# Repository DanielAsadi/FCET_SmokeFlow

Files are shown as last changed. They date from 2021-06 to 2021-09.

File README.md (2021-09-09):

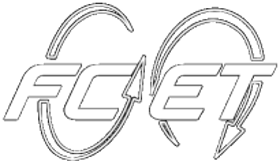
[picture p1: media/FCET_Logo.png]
#  Smoke Flow Visualization Setup
This set of code is for the control of the smoke flow visualization experimental setup at the FCET lab wind tunnel in UTIAS. 
Using an Arduino which receives input from the user or active grid encoder, the circuit outputs timed controls to the valve, heated nichrome wire and camera to create and photograph the smoke flow.

## Further Information
### [Project Information + Progress Document](https://docs.google.com/document/d/1TpjQxDYd5ZbAC--HKGrwxiYLXjzm-MVlI9GUeiGMbgY/edit?usp=sharing)
### [Project Presentation](https://docs.google.com/presentation/d/1Sq_wyhLVnCP48-y7gE646tIXf9qmjQ5rv_RyZEfXHPY/edit?usp=sharing)

### Project Abstract: Automation of a Wind Tunnel Smoke Flow Visualization (SFV) Rig
When analyzing the properties and features of flow around aerodynamic devices, there are quantitative techniques such as particle image velocimetry (PIV) and hot-wire anemometry, while the SFV method provides a simpler set-up and qualitative look at the flow field. The SFV technique consists of a nichrome wire that is coated in propylene glycol and is heated to create lines of smoke through the wind tunnel. It allows for the visual identification of key features such as boundary layers, laminar or turbulent flow and vortex shedding. Currently, each instrument in the setup is controlled manually and is only effective for flow speeds under 5 m/s, therefore limiting the precision of equipment usage for unsteady conditions and the range of possible cases to study. This project aims to increase the efficiency, precision, and versatility of the SFV setup by automating the components using a microcontroller, as well as implementing capacitors to rapidly discharge high levels of current for usage above 5 m/s. The desired circuit and code design will obtain inputs either from an encoder signal or a manual trigger and output precise, timed controls to the wire heating, the dispensing of propylene glycol, the camera, and the capacitors. Design solutions will be evaluated based on the metrics of usability, compatibility and responsiveness. Ultimately, this system maximized the usage of SFV and aided in the studies of laminar separation bubbles. Through iterative design and evaluation of metrics, the created design was able to produce informative images in a consistent manner while additions are being made to augment the usage of the instruments through the ability to read and save data.

## Code Structure
This code was operated using Ardino code which uses C++ and Python. The Arduino code controls the high/low signals and communication to the smoke flow instruments while the Python code controls the user interface and manual or automated control of these signals.

### Python Environment
This project uses the virutalenv Python environment. The Pyserial package is installed to communicate with the Arduino using Python. Matplotlib and Pandas packages are installed for encoder data graphing The commands below were used to create a virtual envrionment and install the additonal packages.
```
> pip install virtualenv
> python3 -m venv smokeflow
> smokeflow\Scripts\activate.bat
(smokeflow) > pip install pyserial
(smokeflow) > pip install matplotlib
(smokeflow) > pip install pandas
```
## Smoke Flow Circuit Diagram and Experimental Setup Photos
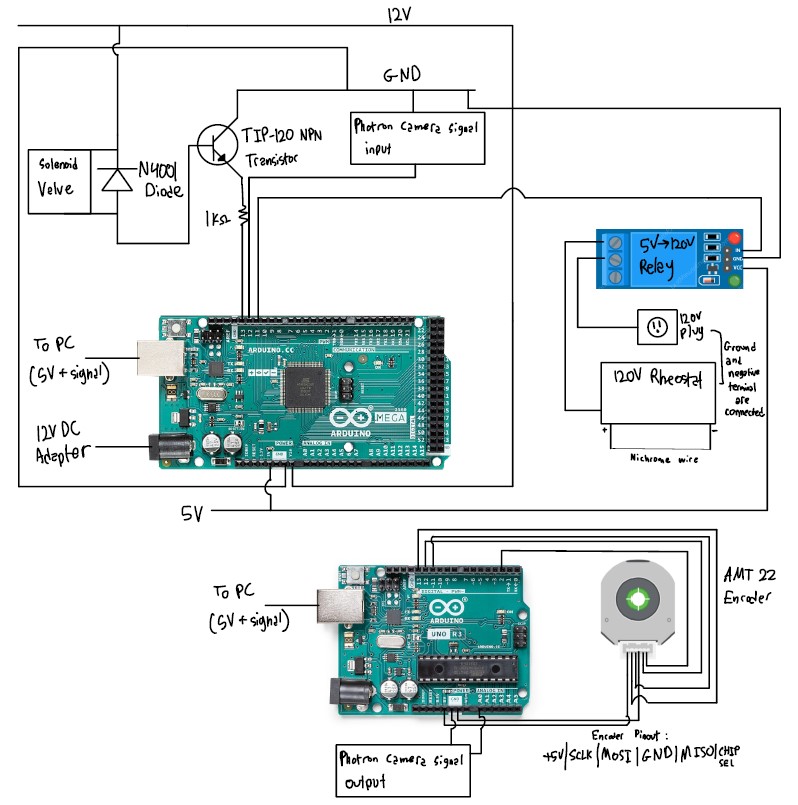
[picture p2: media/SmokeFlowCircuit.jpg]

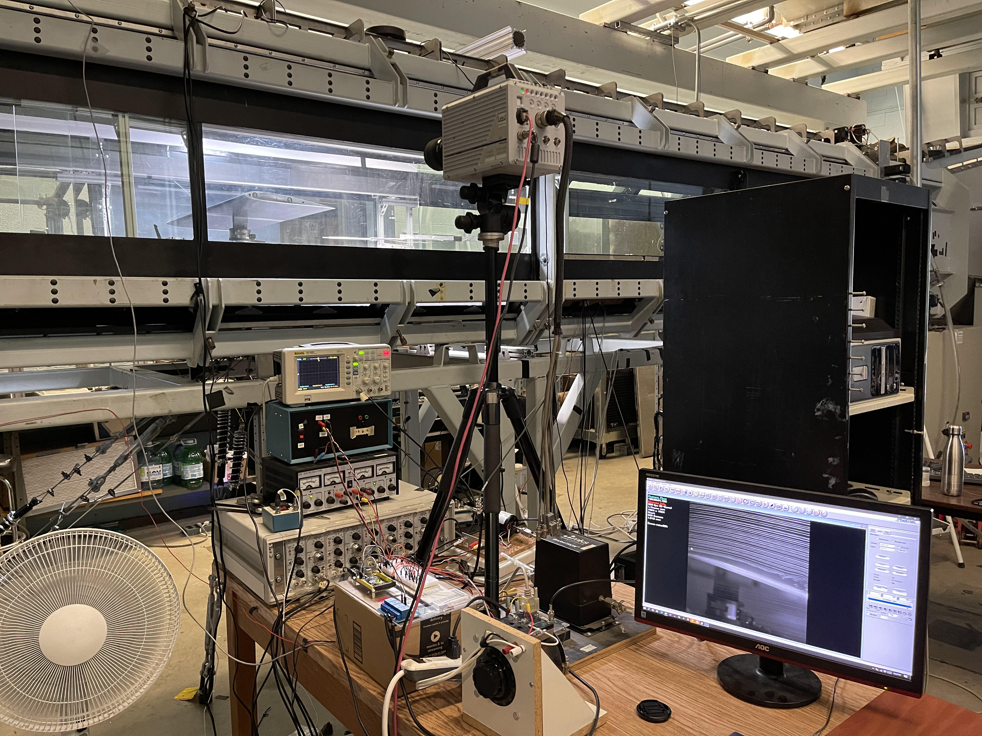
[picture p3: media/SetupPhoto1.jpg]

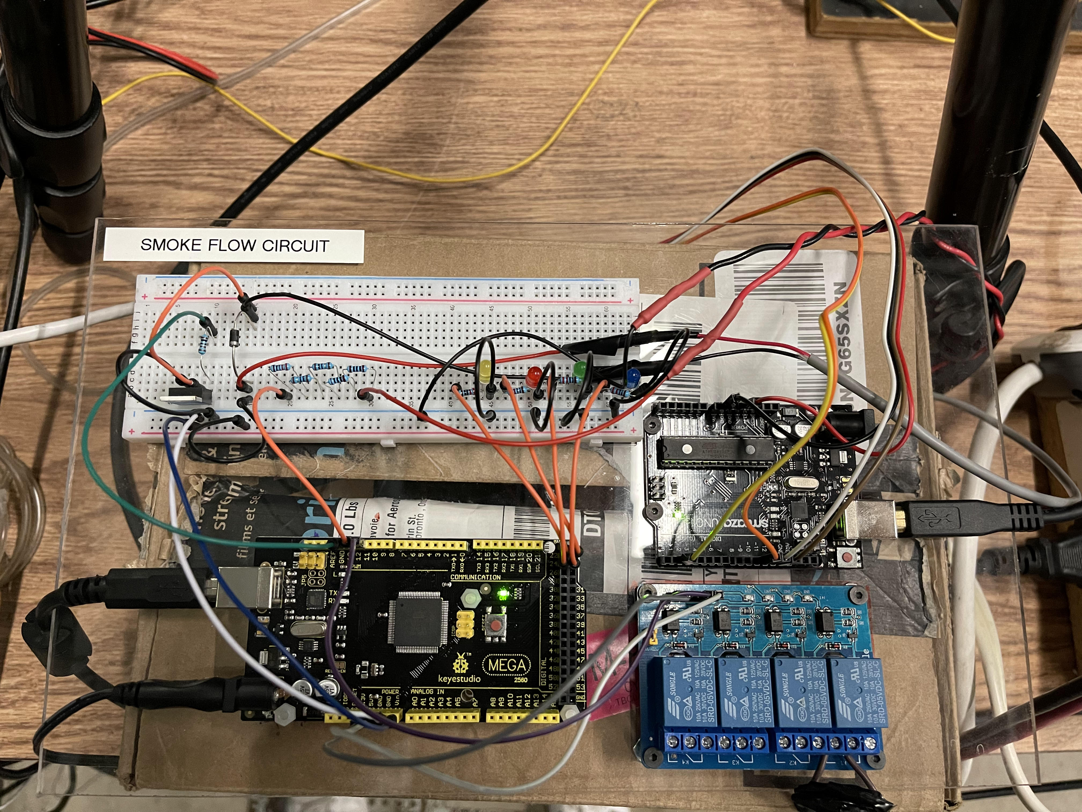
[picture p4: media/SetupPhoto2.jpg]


## Example Smoke Flow Photos
### Re 60k, Alpha 8°, Separation Bubble
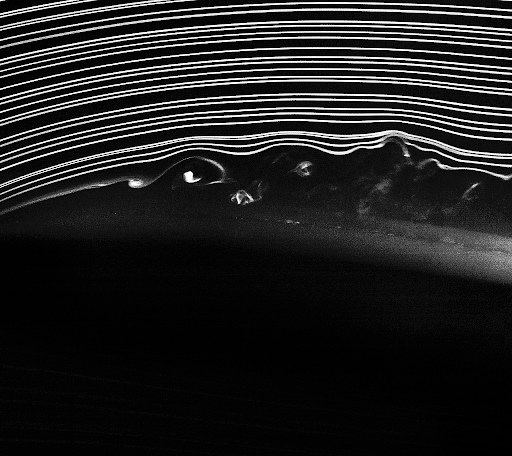
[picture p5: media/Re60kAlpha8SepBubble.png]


### Re 60k, Alpha 4°, Wake
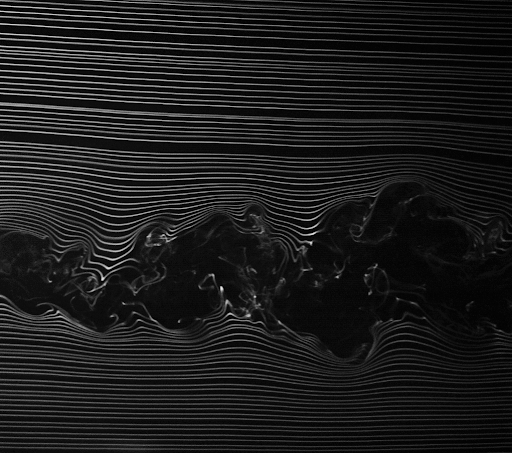
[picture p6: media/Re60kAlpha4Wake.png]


## Other Software Used
PFV4 is used for the control and processing of the photos taken from the high-speed Photron Fastcam SA5

## File Descriptions
* **.vscode**: VS Code setup files
* **__pycache__**: Python cache files
* **arduino/AMT22_SPI_Uno.ino**: Original, unmodified code to read encoder output from CUI Inc. website (not used)
* **arduino/commMega.ino**: Currently used Arduino code with Arduino Mega
* **arduino/encUno.ino**: Code for the second Arduino used which recieves input from the encoder on the active grid
* **data**: Encoder data csv and graph files
* **dataAcquisition/create_csv.py**: Creates csv for encoder data (not used)
* **dataAcquisition/create_plot_phase.py**: Creates phase plot for encoder data, converting time axis
* **dataAcquisition/freq.py**: Interpolates frequency from encoder graph, separate from ctrl_ag version (testing purposes)
* **dataAcquisition/testEnc.py**: Code for just running and testing encoder output performance (testing purposes)
* **media**: Setup diagrams and other pictures
* **info**: PDF documents with resources and information about the project
* **steady/ctrl_V1.py**: Version 1 of Python control code (not used)
* **steady/ctrl_man.py**: Python control code with componenets manually triggered on/off by user
* **steady/ctrl_seq.py**: Python control code with timed sequence controlling all compoenents automatically
* **unsteady/ctrl_ag.py**: Python control code for unsteady case with active grid and encoder and graphing ability in burst mode
* **unsteady/ctrl_ag_V1.py**: Version 1 of Python control code for unsteady case with active grid and encoder (not used)
* **unsteady/ctrl_ag_cont.py**: Python control code for unsteady case with active grid and encoder and graphing ability in continuous mode
* **unsteady/ctrl_ag_live.py**: Runs control_ag_V1.py and create_plot_phase.py for live plotting using threading and subprocess (not used)
* **unsteady/ctrl_ag_low_freq.py**: Python control code for unsteady case with active grid and encoder and graphing ability in burst mode triggered at specified phase angle

## Version Status
### v1
This version supports manual and automated control for steady-state conditions under 5m/s without the active grid or capacitors
### v2
This current version supports v1.0 features and automated control triggered by the active grid encoder with a second Arduino with encoder data acquisition capabilities
### v3
This future version will implement capacitors to allow operations at flow speeds above 5 m/s

## Contributors
Project by: Daniel Asadi, University of Toronto, Division of Engineering Science

Assisted by: Daniel Foster, University of Toronto, Division of Engineering Science

Supervised by: Suraj Banal, PhD Candidate, FCET Lab, UTIAS and Professor Philippe Lavoie, FCET Lab, UTIAS

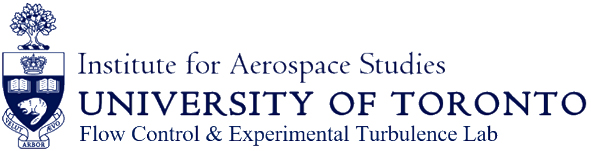
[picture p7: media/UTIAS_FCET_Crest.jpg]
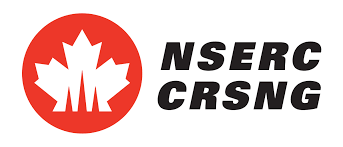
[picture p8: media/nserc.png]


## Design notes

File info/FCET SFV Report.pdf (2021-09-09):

Daniel Asadi | FCET UTIAS 2021

# FCET SMOKE FLOW VIZ RESEARCH

Github Link | 1
Presentation Link | 1
Project Abstract | 2
Encoder Research | 3
Types of Encoders | 3
Encoder Technologies | 3
Current Experimental Setup | 4
Code and Arduino Resources | 4
Smoke Flow Literature Review | 4
Camera Alternatives | 5
Smoke Flow Components Resources | 5
Experimental Setup Notes | 6
Smoke Flow Setup Specifics | 6
Future/In progress work | 6
Progress Log | 8
Experimental Setup Photos | 11
Additional Resources | 14

## Github Link (https://github.com/DanielAsadi/FCET_SmokeFlow)

Presentation Link (https://docs.google.com/presentation/d/1Sq_wyhLVnCP48-y7gE646tIXf9qmjQ5rv_RyZEfXHPY/edit?usp=sharing)

## Project Abstract

Automation of a Wind Tunnel Smoke Flow Visualization (SFV) Rig When analyzing the properties and features of flow around aerodynamic devices, there are quantitative techniques such as particle image velocimetry (PIV) and hot-wire anemometry, while the SFV method provides a simpler set-up and qualitative look at the flow field. The SFV technique consists of a nichrome wire that is coated in propylene glycol and is heated to create lines of smoke through the wind tunnel. It allows for the visual identification of key features such as boundary layers, laminar or turbulent flow and vortex shedding. Currently, each instrument in the setup is controlled manually and is only effective for flow speeds under 5 m/s, therefore limiting the precision of equipment usage for unsteady conditions and the range of possible cases to study. This project aims to increase the efficiency, precision, and versatility of the SFV setup by automating the components using a microcontroller, as well as implementing capacitors to rapidly discharge high levels of current for usage above 5 m/s. The desired circuit and code design will obtain inputs either from an encoder signal or a manual trigger and output precise, timed controls to the wire heating, the dispensing of propylene glycol, the camera, and the capacitors. Design solutions will be evaluated based on the metrics of usability, compatibility and responsiveness. Ultimately, this system maximized the usage of SFV and aided in the studies of laminar separation bubbles. Through iterative design and evaluation of metrics, the created design was able to produce informative images in a consistent manner while additions are being made to augment the usage of the instruments through the ability to read and save data.

## Encoder Research

- “Encoders are sensing devices whose purpose is to provide feedback about the motion of objects to control systems. This feedback allows the control system to establish whether the object being monitored is being correctly moved or positioned and permits adjustments to be made or actions to be taken based on the movement and position of the object.”
- Selection considerations
- Environmental conditions, vibration
- Resolution
- Size
- Design/compatibility

## Types of Encoders

- Linear Encoders
- Rotary Encoders
- Angle Encoders
- Absolute Encoders
- Incremental Encoders

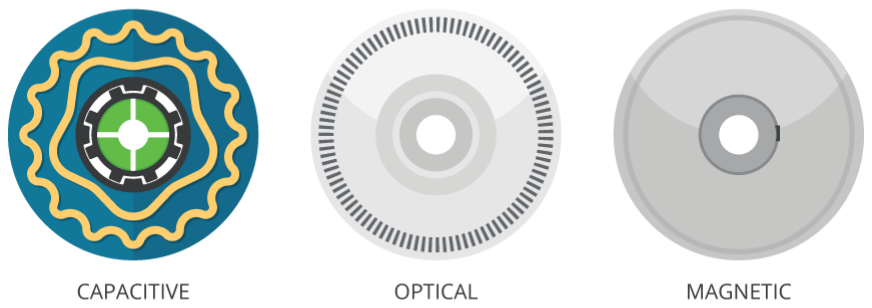
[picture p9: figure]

- https://www.thomasnet.com/articles/automation-electronics/types-of-encoders-a-thomasnet-buying-guide/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 e%20most,lines%20and%20alternating%20translucent%20slots (https://www.thomasnet.com/articles/automation-electronics/types-of-encoders-a-thomasnet-buying-guide/)

## Encoder Technologies

- Magnetic
- Optical
- Capacitive
- https://www.cuidevices.com/blog/capacitive-magnetic-and-optical-encoder s-comparing-the-technologies (https://www.cuidevices.com/blog/capacitive-magnetic-and-optical-encoders-comparing-the-technologies)
| Capacitive | Optical | Magnetic
Resistance to Dirt, Dust, Oil | High | Low | High
Accuracy | High | High | Low
Temperature Range | Wide | Medium | Narrow
Current Consumption | Low | High | Medium
Programmability | Yes | No | No
Package Size | Small | Medium | Medium
EMC Immunity | High | High | High
Magnetic Immunity | High | High | Low
Resolution Range | Wide | Wide | Narrow

## Current Experimental Setup

- Encoder: AMT22 Series, 28 mm, 14 Bit, Single-Turn, Absolute, SPI Interface, Capacitive Modular Encoder, AMT Viewpoint software
- Microcontroller: Arduino Mega, Arduino Uno
- Active grid motor: STM 23S-3RN
- Camera: Photron Fastcam SA5
- Valve: 12V DC solenoid valve
- Wire: 30 AWG Nichrome wire

## Code and Arduino Resources

- https://pythonforundergradengineers.com/python-arduino-potentiometer. html (https://pythonforundergradengineers.com/python-arduino-potentiometer.html)
- https://makersportal.com/blog/2018/2/25/python-datalogger-reading-the-s erial-output-from-arduino-to-analyze-data-using-pyserial (https://makersportal.com/blog/2018/2/25/python-datalogger-reading-the-serial-output-from-arduino-to-analyze-data-using-pyserial)
- https://pythonforundergradengineers.com/python-arduino-LED.html

## Smoke Flow Literature Review

- Papers from:
- https://drive.google.com/drive/folders/17lmvIWtnZ_uoro7y_4VE0kZJ-q3x1EDU?usp=sharing (https://drive.google.com/drive/folders/17lmvIWtnZ_uoro7y_4VE0kZJ-q3x1EDU?usp=sharing)
- Paper 1
- Camera: Canon 5D Mark II DSLR
- Sens: ISO-100
- Aperture: F6.3
- Shutter speed: 1/200s
- Flash: Canon 600EX-RT, 1/128 of max power output, flash duration of 100µs measured using an optical-to-electrical analog converter (Tektronix P6701B)
- Paper 2 (Used laser sheet)
- Camera: FAST-CAM SA-3 which records images up to 60,000 fps, with an internal memory of 4 GB, only max FPS of 250 was used, lower frame rates were also used, so the authors believe that these images could have been obtained with a standard camera
- Lens: Nikon 105-mm lens (model AF Micro Nikkor 105 mm)
- Aperture: F/2.8
- Paper 3 (Used laser sheet)
- Camera: commercial digital camera with a snapshot resolution of 4,000 × 6,000 pixels and a 50 Hz video recording resolution of 720 × 1280 pixels during the smoke flow visualization
- Manual operation
- Paper 4
- Camera: Nikon D70s DSLR
- 4 FPS

- Flash: Nikon SB 800 Speedlight
- Paper 5
- Camera: Nikon D70s digital camera which acquired four consecutive images per second with an image resolution of six megapixels
- Flash: Nikon SB 800 Speedlight, i.e., a high-speed flash, which was triggered wirelessly by the camera

## Camera Alternatives

- Imager SCMOS
- Datasheet in drive
- Stingray F125B
- Pin 7 gnd (black) and pin 4 trigger (red)
- Vimba software
- Manuals in drive
- https://www.alliedvision.com/en/products/software.html
- https://github.com/alliedvision/VimbaPython
- DSLR Camera
- https://www.youtube.com/watch?v=oQkVPrsatbQ&t=717s&ab_channel=VecVideosVecVideos (https://www.youtube.com/watch?v=oQkVPrsatbQ&t=717s&ab_channel=VecVideosVecVideos)
- https://www.youtube.com/watch?v=_ZOJiIvAwBE&ab_channel=SunPixe lVideo (https://www.youtube.com/watch?v=_ZOJiIvAwBE&ab_channel=SunPixelVideo)
- http://www.doc-diy.net/photo/remote_pinout/
- Photron Camera
- Manuals in drive
- https://www.youtube.com/watch?v=cLVt1M9vAzw&t=31s&ab_channel=P hotronMarketing (https://www.youtube.com/watch?v=cLVt1M9vAzw&t=31s&ab_channel=PhotronMarketing)
- https://photron.com/photron-support/
- PFV4 software
- Ethernet connection to pc
- Connect to “TRIG TTL IN” BNC cable

## Smoke Flow Components Resources

- Valve
- http://bc-robotics.com/tutorials/controlling-a-solenoid-valve-with-arduino/ (http://bc-robotics.com/tutorials/controlling-a-solenoid-valve-with-arduino/)
- Camera
- https://drive.google.com/drive/folders/1uzS8pdFq9TwNUtFZqKad7nzDRWsV8fpy?usp=sharing (https://drive.google.com/drive/folders/1uzS8pdFq9TwNUtFZqKad7nzDRWsV8fpy?usp=sharing)
- Wire, (powered using 120v to 5V relay to Arduino)
- https://lastminuteengineers.com/one-channel-relay-module-arduino-tutorial/ (https://lastminuteengineers.com/one-channel-relay-module-arduino-tutorial/)
- Capacitors
- https://www.electronics-tutorials.ws/rc/rc_1.html

- https://www.electronics-tutorials.ws/rc/rc_2.html
- Encoder
- https://www.cuidevices.com/product/resource/sample-code/amt22

## Experimental Setup Notes

1. Reynolds number range 60,000, 100,000, AOAs of 4deg and 8deg and 15deg for each (steady-state)
2. Repeat 1 with turbulence grids
3. Run unsteady cases for Re= 60,000 and alpha=15 and k=0.01, 0.05, 0.1, 0.4, 0.7, 1, 1.2, 1.5
4. For k=0.01 and 0.05 do the highest amplitude case and 10% amplitude
5. Look at reattachment and how they evolve downstream, unsteady vortex shedding and how it gets affected by free-stream turbulence
6. Clean tunnel, smallest grid, bigger grid if time permits
7. Improve beads uniformity, wire smoothness and tension
8. Optimize lighting

## Smoke Flow Setup Specifics

- Propylene glycol:
https://www.amazon.ca/dp/B076FCWZZ6/ref=cm_sw_r_oth_api_glt_i_AD2YF0B3D9KRYWSDD21R?_encoding=UTF8&psc=1 (https://www.amazon.ca/dp/B076FCWZZ6)
- Used 2kg of weights to straighten nichrome wire
- Used Allen key to wrap wire at the bottom as it does not deform
- Connect circuit to camera’s “TRIG TTL IN” BNC cable
- PFV settings
- Live mode after recording
- Configuration>Trigger>Direct Trigger
- I/O> TRIG TTL IN> TRIG POS
- Choose frame rate, do calibration, focus on the frame, then you are ready for recording
- Frequently wipe funnel and under it as well as wire to prevent leaks
- Use Windex and microfiber cloth to clean test section glass
- Zeroing encoder position: Re-upload encUno arduino program twice, once with line 82 uncommented and once with line 82 commented before starting active grid
- Encoder mounting:
https://www.youtube.com/watch?v=NNBdfpqhKBI&ab_channel=CUIDevices

## Future/In progress work

- Capacitors implementation for trials over 5m/s
- https://www.electronics-tutorials.ws/rc/rc_1.html
- https://www.electronics-tutorials.ws/rc/rc_2.html
- https://www.youtube.com/watch?v=GrvvkYTW_0k&ab_channel=AddOh ms (https://www.youtube.com/watch?v=GrvvkYTW_0k&ab_channel=AddOhms)

- https://www.youtube.com/watch?v=3PkpOeHTnfo&ab_channel=Indrek
- Report/Documentation
- Setup/code guide
- Summary of summer work
- More github documentation
- Add pdfs to github
■ FCET SFV Abstract
■ FCET SFV Documentation
■ FCET SFV Presentation
■ FCET SFV Summary
- Low priority
- Snubber/Diode because of 5v relay resetting circuit
- Really fast input - port manipulation
■ https://forum.arduino.cc/t/reading-really-fast-digital-input/204463/7 (https://forum.arduino.cc/t/reading-really-fast-digital-input/204463/7)
■ https://www.instructables.com/Arduino-and-Port-Manipulation/ (https://www.instructables.com/Arduino-and-Port-Manipulation/)
- https://gfm.aps.org/ (Deadline: Sept. 17)
- Read encoder values after 1s of starting readline so the beginning of graph is not glitched

## Progress Log

Week | Work done | Notes
1 | Administrative Stuff | -Review papers from Prof. Lavoie
2 | Researched Papers, learned Arduino, python implementation
3 | Researched encoders, connected encoder to read position | -Check min delay required for encoder code -Look into what coupling to use to address the issue
4 | Implemented code into python and lit LED if encoder value is within a range as a proof of concept for the input and output which will later be camera/valve/wire | -Remember to change the COM port -Remember to be in conda env
5 | Researched cameras, experimental setups, camera to Arduino connection, connected solenoid valve to circuit + code using transistor, diode and resistor, added Stingray F125B camera to the circuit, learned its software | -Draw a circuit for the valve and camera -Find what camera to use -Slightly over 12V power supply -NE555 timing chip? -Potentiometer to adjust time interval? -Blink without delay for camera delay -Put stuff into methods -Look into really fast input
6 | Read through stingray camera’s manuals and python API, changed the camera to Imager SCMOS and learned its control, started setting up an experimental setup | -Research python API -Research how to control, trigger methods
7 | Had a meeting with Phil, set up experimental smoke flow viz setup with wire, valve, Photron camera connected to my pc, rheostat and Arduino, changed Arduino Uno to mega, created manual mode python code and improved active grid mode, improved and organized general code on Arduino | -Replace wire, optimize voltage, look into controlling rheostat -Had short circuit and therefore had to replace some parts, fixed cable management and insulating wires to prevent the issue
8 | Took some smoke flow viz case photos, replaced valve, created code that does smoke flow setup in a sequence automatically, installed | -See serial issue in code, fix pfv4 software issues -Fix coding issues in comments

5v relay for rheostat, researched capacitor usage, researched how to improve oil beads on the wire to improve streamlines quality

9 Worked on improving setup, improved wire using weights to straighten it and thus bead uniformity resulting in visualization of the separation bubble, created GitHub, had a meeting with Phil, figured out camera frames issue - has something to do with changing to external trigger mode having too high current - reduced current to recommended range using resistors, removed encoder code from Arduino to prevent the serial lag issue, did Re60k, Re100k trials, improved code and made it more user-friendly, there is smooth experimental setup and automation now

To do:
-Draw circuit diagrams✅
-Look into pfv4 software issue vs pfv3✅
-Mount 5v relay to board✅
-Fix pfv3 ext trigger not working✅ -Look into setup with smaller wind tunnel✅
-Camera signal emitting 80mA, should be below 30 - can fix by increasing resistance or
decreasing voltage✅
-Why does the valve turn on and off when running the program at the start-> need a diode or snubber?
-Add a second Arduino just for the encoder to run separately and not fill up serial, can run from the same python program maybe, but with different terminals running at the same time
-Add code for a sequence that asks if bead formation is good, if not, dispense liquid again✅
10 | Updated Github, set up code on lab pc so you can use code and pfv4 from the same device, used calibration target to measure distances and scale and enhance zoom focus, took more alpha=4,8 and Re=60k,100k cases | -Add parameter in code for Reynolds number, to change delays, use comments from lab pc code -Add option for if oil is already on the wire -Tighten the wire like a guitar string tightener? -Camera getting signal from wire signal -> need a snubber/diode?
11 | N/A | N/A
12 | Finished GitHub setup, readme, helped Daniel M. with PIV glass component, edited smoke flow pics with photoshop, worked on fixing encoder issue, added 2nd Arduino for the encoder, updated code and circuit for encoder usage, installed encoder on active grid motor | -Remove encoder code from Arduino Mega code, not necessary

13 | Started work on adding python code to record, save and display live encoder data in CSV and graph form
14 | Continued work on encoder data, fixed encoder positioning on active grid axle to not be in the way of the axle coupling, added ability to read when the camera starts recording in order to find delays in recording to record a phase at the correct starting time, prepared final version of UnERD abstract | -Update readme, GitHub code, circuit graph, add media section, -Rewrite Arduino mega code -Fix filename feature, -Snubber/diode for 5v relay -Take updated circuit photos
15 | Started taking unsteady cases with active grid, fixed recording issues and delays with code
16 | Worked on capacitors implementation, UnERD presentation, and documentation

## Experimental Setup Photos

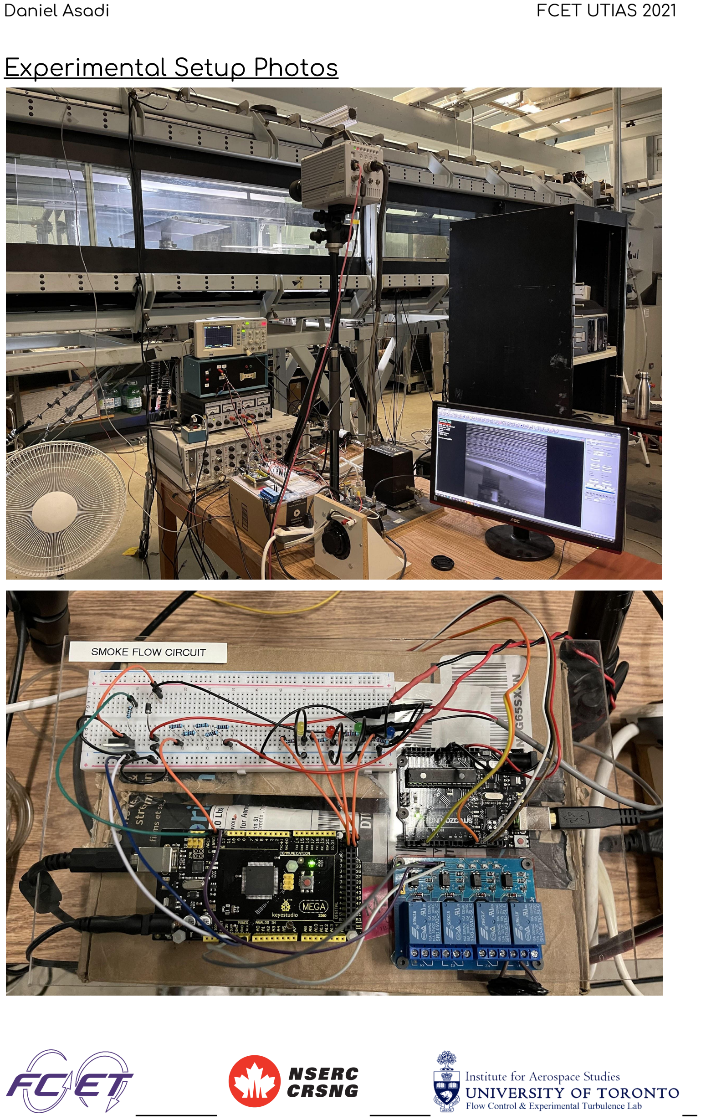
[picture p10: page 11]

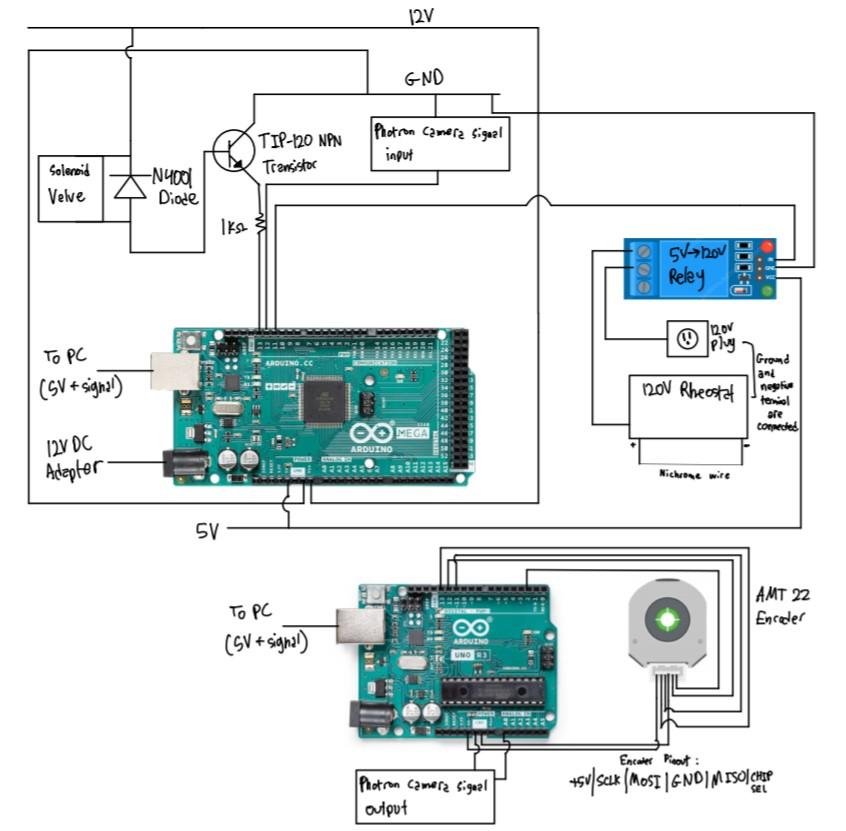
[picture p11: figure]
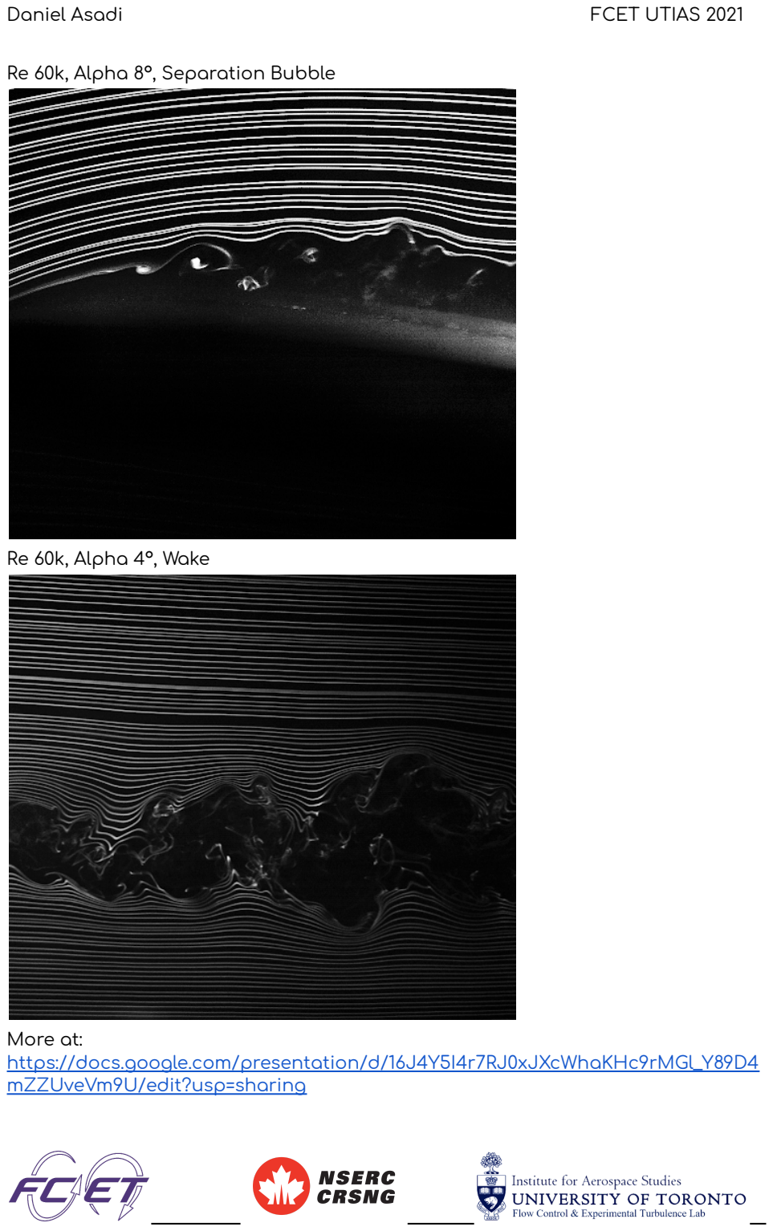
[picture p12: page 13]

Re 60k, Alpha 8°, Separation Bubble

Re 60k, Alpha 4°, Wake

More at:
https://docs.google.com/presentation/d/16J4Y5I4r7RJ0xJXcWhaKHc9rMGl_Y89D4mZZUveVm9U/edit?usp=sharing (https://docs.google.com/presentation/d/16J4Y5I4r7RJ0xJXcWhaKHc9rMGl_Y89D4mZZUveVm9U/edit?usp=sharing)

## Additional Resources

- https://www.cuidevices.com/resources/resource-library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 (https://www.cuidevices.com/resources/resource-library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)
- https://www.cuidevices.com/product/motion/rotary-encoders/absolute/modular/amt22-series (https://www.cuidevices.com/product/motion/rotary-encoders/absolute/modular/amt22-series)
- https://www.mcmaster.com/
- https://www.digikey.ca/

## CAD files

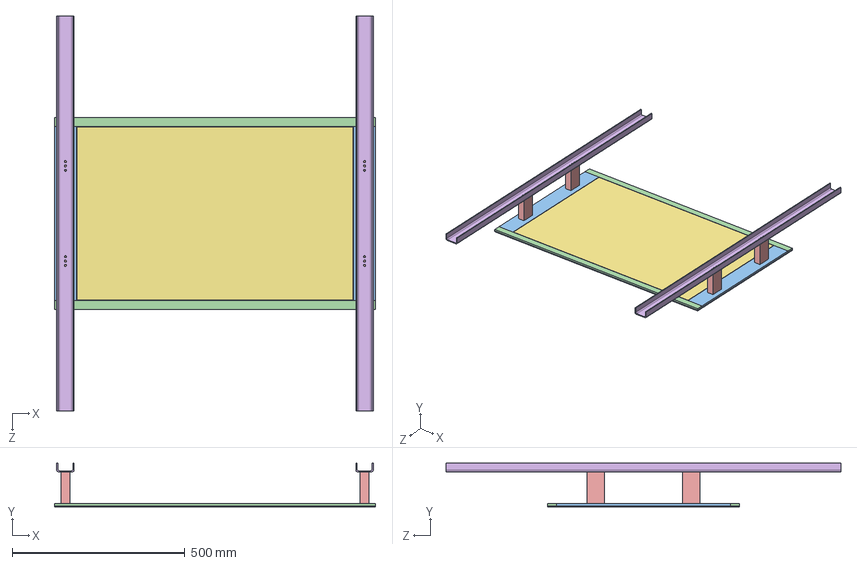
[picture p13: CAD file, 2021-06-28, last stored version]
PIV/PanelFrame.SLDASM
930.0 x 127.0 x 1143.0 mm
CeilingPanel2 x 2
CeilingPanel1 x 2
CeilingPanel3 x 2
CeilingPanel4 x 2
PanelColumns x 4
C-Channel x 2
CeilingGlassPanel

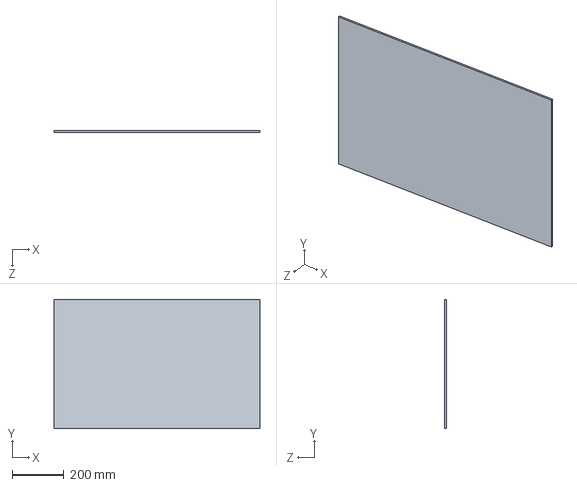
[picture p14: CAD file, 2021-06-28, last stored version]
PIV/CeilingGlassPanel.SLDPRT
800.1 x 501.6 x 6.35 mm

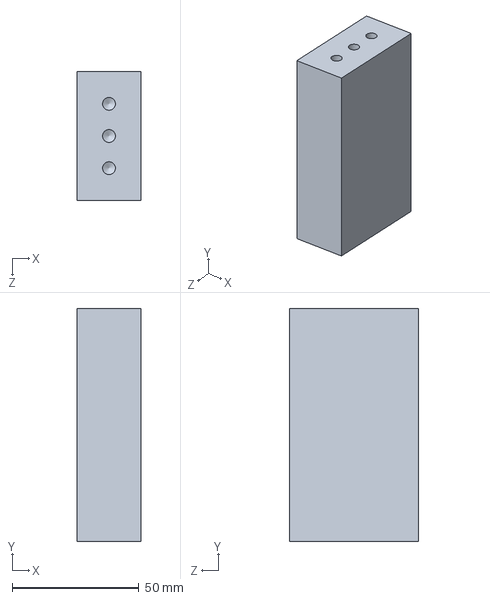
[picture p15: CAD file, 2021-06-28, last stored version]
PIV/PanelColumns.SLDPRT
25.4 x 92.1 x 50.8 mm

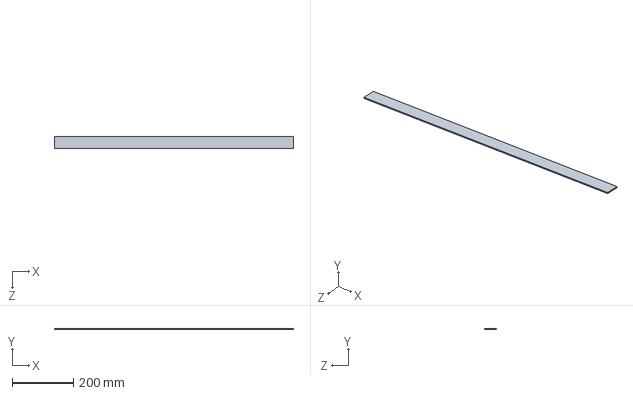
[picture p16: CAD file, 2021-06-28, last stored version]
PIV/CeilingPanel2.SLDPRT
777.6 x 3.17 x 38.1 mm

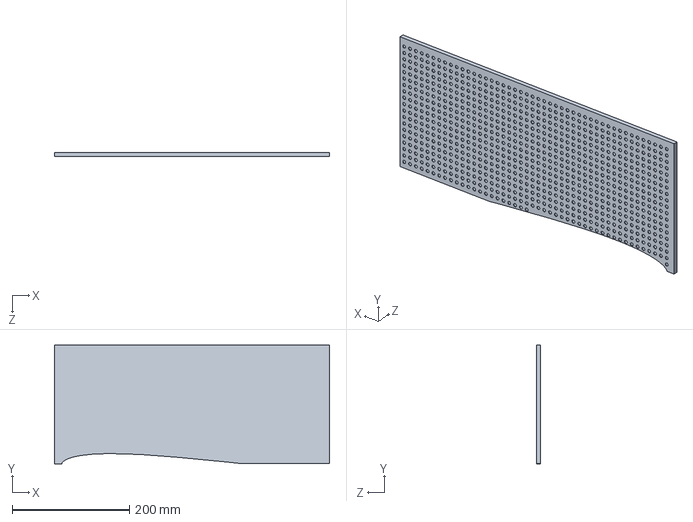
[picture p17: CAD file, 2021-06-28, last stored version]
PIV/Calibration_Target.SLDPRT
469.9 x 203.2 x 6.35 mm

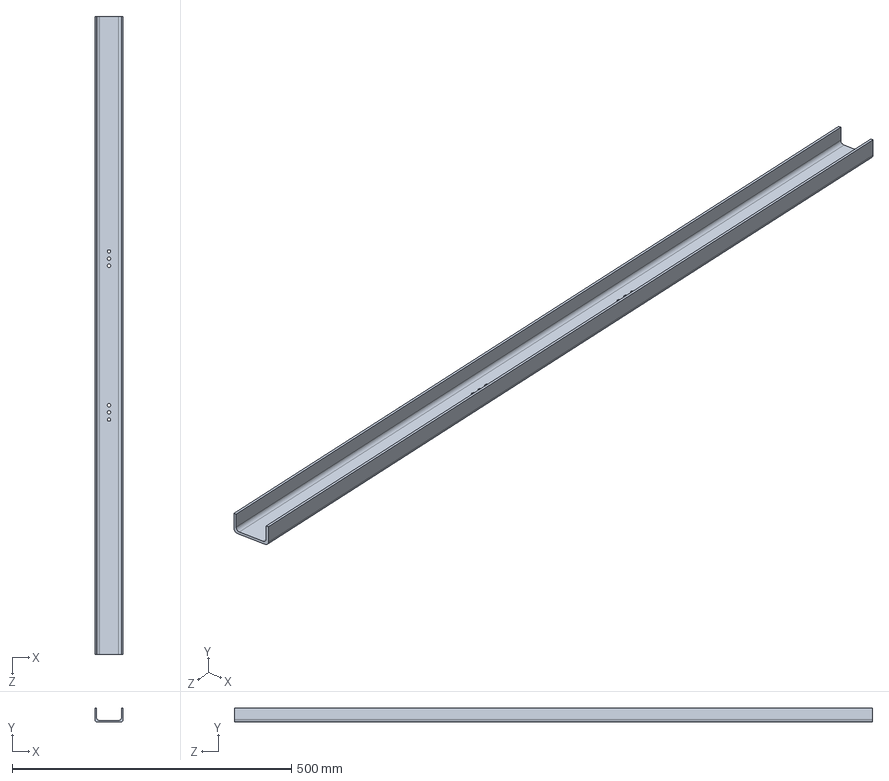
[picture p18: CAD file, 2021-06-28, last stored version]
PIV/C-Channel.SLDPRT
50.8 x 25.4 x 1143.0 mm

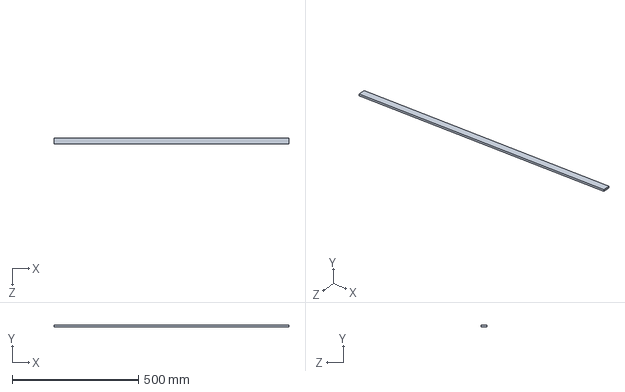
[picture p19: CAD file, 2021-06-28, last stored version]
PIV/CeilingPanel4.SLDPRT
930.0 x 6.35 x 25.4 mm

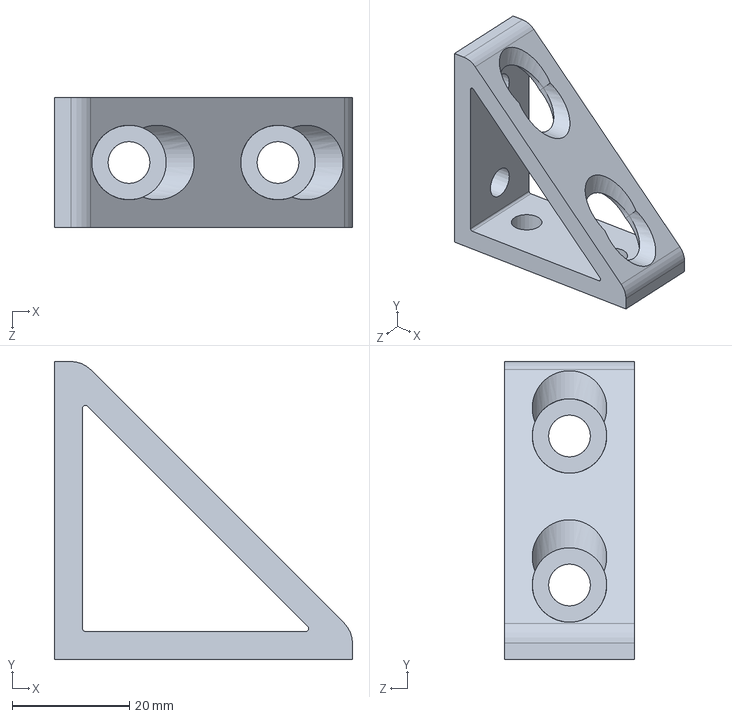
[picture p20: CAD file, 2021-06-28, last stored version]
PIV/8020-4136-BLACK.SLDPRT
50.8 x 50.8 x 22.2 mm

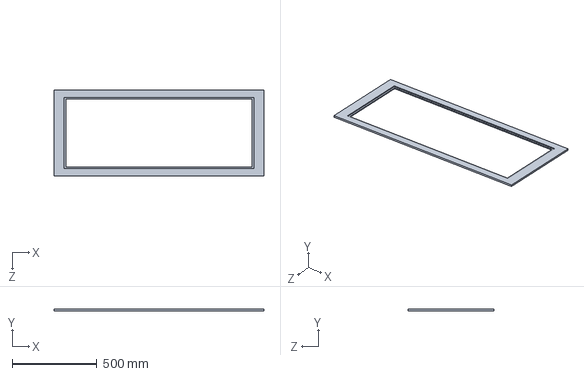
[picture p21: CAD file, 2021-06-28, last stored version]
PIV/CeilingPanel.SLDPRT
1240.0 x 10.0 x 505.0 mm

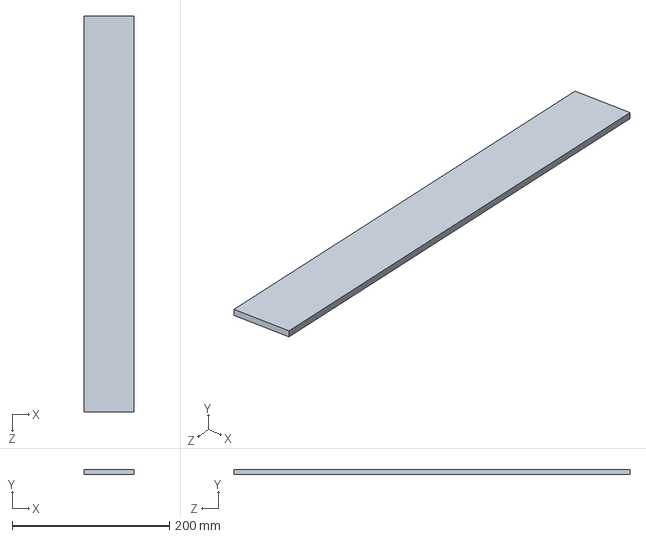
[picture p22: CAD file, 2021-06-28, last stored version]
PIV/CeilingPanel3.SLDPRT
63.5 x 6.35 x 504.2 mm

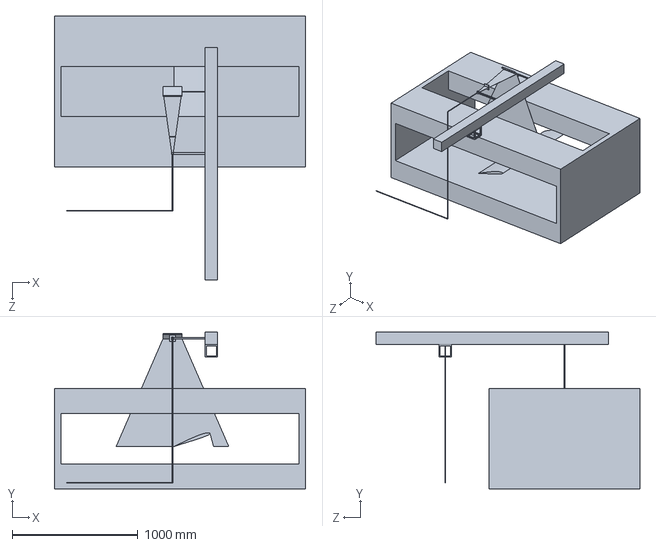
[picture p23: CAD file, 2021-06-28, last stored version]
PIV/PIV_Arrangement.SLDPRT
2000.0 x 1250.0 x 2100.0 mm

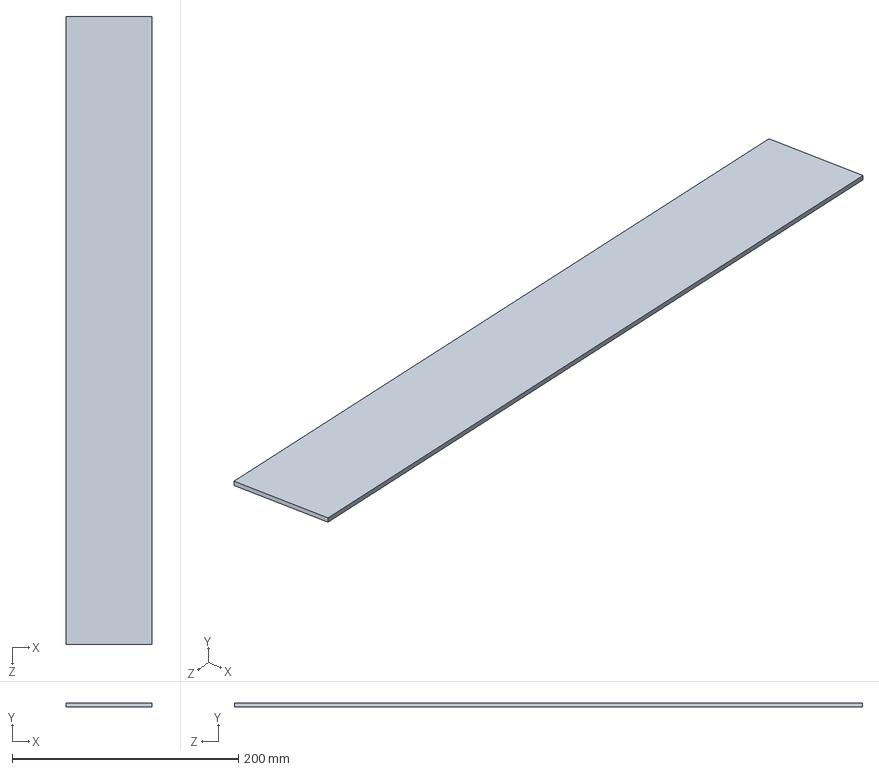
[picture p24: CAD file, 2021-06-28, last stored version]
PIV/CeilingPanel1.SLDPRT
76.2 x 3.17 x 555.0 mm

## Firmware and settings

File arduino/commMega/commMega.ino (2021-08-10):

//Daniel Asadi
//Eng Sci 2T3
//FCET Lab, UTIAS
//From code created by Jason Kelly at CUI Inc.

/* MANUAL CONTROL FOR MEGA
   Set the baud rate to 115200 to view the serial stream the position from the AMT22.

   Arduino Pin Connections
   SPI Chip Select Enc 0:   Pin  2
   SPI Chip Select Enc 1:   Pin  3
   SPI MOSI                 Pin 11
   SPI MISO                 Pin 12
   SPI SCLK:                Pin 13

   AMT22 Pin Connections
   Vdd (5V):                Pin  1 RED
   SPI SCLK:                Pin  2 BROWN
   SPI MOSI:                Pin  3 ORANGE
   GND:                     Pin  4 BLACK
   SPI MISO:                Pin  5 GREEN
   SPI Chip Select:         Pin  6 YELLOW
*/

/* Include the SPI library for the arduino boards */
#include <SPI.h>

/* Serial rates for UART */
#define BAUDRATE 115200

/* SPI commands */
#define AMT22_NOP 0x00
#define AMT22_RESET 0x60
#define AMT22_ZERO 0x70

/* Define special ascii characters */
#define NEWLINE 0x0A
#define TAB 0x09

/* We will use these define macros so we can write code once compatible with 12 or 14 bit encoders */
#define RES12 12
#define RES14 14

/* SPI pins */
#define ENC_0 32    //YELLOW CABLE
#define ENC_1 1     //ALT ENCODER, NOT USED RN
#define SPI_MOSI 51 //ORANGE CABLE
#define SPI_MISO 50 //GREEN CABLE
#define SPI_SCLK 52 //BROWN CABLE
#define LEDY 22     //VALVE STATUS
#define LEDR 23     //CAM STATUS
#define LEDG 24     //WIRE STATUS
#define LEDB 25     //CAP STATUS
#define VALVE 13    //PWM
#define CAM 12      //PWM
#define WIRE 11     //PWM
#define CAP 10      //PWM
#define CAMOUT A0 //CAM RECORDING OUTPUT

//create a 16 bit variable to hold the encoders position
uint16_t encoderPosition;
//let's also create a variable where we can count how many times we've tried to obtain the position in case there are errors
uint8_t attempts;

int incomingByte; // a variable to read incoming serial data into

void setup()
{
  digitalWrite(WIRE, HIGH); //Set wire off by default
  digitalWrite(VALVE, LOW); //Set valve off by default
  //Set the modes for the SPI IO
  pinMode(SPI_SCLK, OUTPUT);
  pinMode(SPI_MOSI, OUTPUT);
  pinMode(SPI_MISO, INPUT);
  pinMode(ENC_0, OUTPUT);
  pinMode(ENC_1, OUTPUT);
  pinMode(LEDY, OUTPUT);
  pinMode(LEDR, OUTPUT);
  pinMode(LEDG, OUTPUT);
  pinMode(LEDB, OUTPUT);
  pinMode(VALVE, OUTPUT);
  pinMode(CAM, OUTPUT);
  pinMode(WIRE, OUTPUT);
  pinMode(CAP, OUTPUT);

  //Initialize the UART serial connection for debugging
  Serial.begin(BAUDRATE);
  Serial.setTimeout(50);

  //Get the CS line high which is the default inactive state
  digitalWrite(ENC_0, HIGH);
  digitalWrite(ENC_1, HIGH);

  //set the clockrate. Uno clock rate is 16Mhz, divider of 32 gives 500 kHz.
  //500 kHz is a good speed for our test environment
  //SPI.setClockDivider(SPI_CLOCK_DIV2);   // 8 MHz
  SPI.setClockDivider(SPI_CLOCK_DIV4); // 4 MHz
  //SPI.setClockDivider(SPI_CLOCK_DIV8);   // 2 MHz
  //SPI.setClockDivider(SPI_CLOCK_DIV16);  // 1 MHz
  //SPI.setClockDivider(SPI_CLOCK_DIV32);  // 500 kHz
  //SPI.setClockDivider(SPI_CLOCK_DIV64);  // 250 kHz
  //SPI.setClockDivider(SPI_CLOCK_DIV128); // 125 kHz

  //start SPI bus
  SPI.begin();
}

void loop()
{
  //if you want to set the zero position before beggining uncomment the following function call
  //setZeroSPI(ENC_0);
  //setZeroSPI(ENC_1);
  /*int camOutput = analogRead(CAMOUT);
  float voltage = camOutput * (5.0 / 1023.0);
  if(voltage > 4){
    digitalWrite(LEDB, HIGH);    
  }
  else{
    digitalWrite(LEDB, LOW);
  }
  Serial.println(voltage);*/
  /* TEMPPPPPPPPPPPPPPPPPPPPPPPPPPPPPPPPPPPPPPPPPPPPPPPPPPPPPPPPPPPPPPPPPPPPPPPPPPPPPPPPPPPPPPPPPPPPPPPPPPPPPPPP
  attempts = 0; //set attemps counter at 0 so we can try again if we get bad position

  //this function gets the encoder position and returns it as a uint16_t
  //send the function either res12 or res14 for your encoders resolution
  encoderPosition = getPositionSPI(ENC_0, RES14);

  //if the position returned was 0xFFFF we know that there was an error calculating the checksum
  //make 3 attempts for position. we will pre-increment attempts because we'll use the number later and want an accurate count
  while (encoderPosition == 0xFFFF && ++attempts < 3){
    encoderPosition = getPositionSPI(ENC_0, RES14);} //try again
  
  if (encoderPosition == 0xFFFF){ //position is bad, let the user know how many times we tried
    Serial.print("Encoder 0 error. Attempts: ");
    Serial.print(attempts, DEC); //print out the number in decimal format. attempts - 1 is used since we post incremented the loop
    Serial.write("\r\n");}
  
  else { //position was good, print to serial stream
    Serial.println(encoderPosition, DEC);} //print the position in decimal format
  */
  if (Serial.available() > 0)
  {
    incomingByte = Serial.read(); // read the oldest byte in the serial buffer:

    if (incomingByte == 'A')
    {
      digitalWrite(VALVE, HIGH);
      digitalWrite(LEDY, HIGH);
    }
    else if (incomingByte == 'B')
    {
      digitalWrite(VALVE, LOW);
      digitalWrite(LEDY, LOW);
    }

    if (incomingByte == 'C')
    {
      digitalWrite(CAM, HIGH);
      digitalWrite(LEDR, HIGH);
    }
    else if (incomingByte == 'D')
    {
      digitalWrite(CAM, LOW);
      digitalWrite(LEDR, LOW);
    }

    if (incomingByte == 'E')
    {
      digitalWrite(WIRE, LOW);
      digitalWrite(LEDG, HIGH);
    }
    else if (incomingByte == 'F')
    {
      digitalWrite(WIRE, HIGH);
      digitalWrite(LEDG, LOW);
    }

    if (incomingByte == 'G')
    {
      digitalWrite(CAP, HIGH);
      digitalWrite(LEDB, HIGH);
    }
    else if (incomingByte == 'H')
    {
      digitalWrite(CAP, LOW);
      digitalWrite(LEDB, LOW);
    }
  }

  //For the purpose of this demo we don't need the position returned that quickly so let's wait a half second between reads
  //delay(250);   //delay() is in milliseconds
}

/*
   This function gets the absolute position from the AMT22 encoder using the SPI bus. The AMT22 position includes 2 checkbits to use
   for position verification. Both 12-bit and 14-bit encoders transfer position via two bytes, giving 16-bits regardless of resolution.
   For 12-bit encoders the position is left-shifted two bits, leaving the right two bits as zeros. This gives the impression that the encoder
   is actually sending 14-bits, when it is actually sending 12-bit values, where every number is multiplied by 4.
   This function takes the pin number of the desired device as an input
   This funciton expects res12 or res14 to properly format position responses.
   Error values are returned as 0xFFFF
*/
uint16_t getPositionSPI(uint8_t encoder, uint8_t resolution)
{
  uint16_t currentPosition; //16-bit response from encoder
  bool binaryArray[16];     //after receiving the position we will populate this array and use it for calculating the checksum

  //get first byte which is the high byte, shift it 8 bits. don't release line for the first byte
  currentPosition = spiWriteRead(AMT22_NOP, encoder, false) << 8;

  //this is the time required between bytes as specified in the datasheet.
  //We will implement that time delay here, however the arduino is not the fastest device so the delay
  //is likely inherantly there already
  delayMicroseconds(3);

  //OR the low byte with the currentPosition variable. release line after second byte
  currentPosition |= spiWriteRead(AMT22_NOP, encoder, true);

  //run through the 16 bits of position and put each bit into a slot in the array so we can do the checksum calculation
  for (int i = 0; i < 16; i++)
    binaryArray[i] = (0x01) & (currentPosition >> (i));

  //using the equation on the datasheet we can calculate the checksums and then make sure they match what the encoder sent
  if ((binaryArray[15] == !(binaryArray[13] ^ binaryArray[11] ^ binaryArray[9] ^ binaryArray[7] ^ binaryArray[5] ^ binaryArray[3] ^ binaryArray[1])) && (binaryArray[14] == !(binaryArray[12] ^ binaryArray[10] ^ binaryArray[8] ^ binaryArray[6] ^ binaryArray[4] ^ binaryArray[2] ^ binaryArray[0])))
  {
    //we got back a good position, so just mask away the checkbits
    currentPosition &= 0x3FFF;
  }
  else
  {
    currentPosition = 0xFFFF; //bad position
  }

  //If the resolution is 12-bits, and wasn't 0xFFFF, then shift position, otherwise do nothing
  if ((resolution == RES12) && (currentPosition != 0xFFFF))
    currentPosition = currentPosition >> 2;

  return currentPosition;
}

/*
   This function does the SPI transfer. sendByte is the byte to transmit.
   Use releaseLine to let the spiWriteRead function know if it should release
   the chip select line after transfer.
   This function takes the pin number of the desired device as an input
   The received data is returned.
*/
uint8_t spiWriteRead(uint8_t sendByte, uint8_t encoder, uint8_t releaseLine)
{
  //holder for the received over SPI
  uint8_t data;

  //set cs low, cs may already be low but there's no issue calling it again except for extra time
  setCSLine(encoder, LOW);

  //There is a minimum time requirement after CS goes low before data can be clocked out of the encoder.
  //We will implement that time delay here, however the arduino is not the fastest device so the delay
  //is likely inherantly there already
  delayMicroseconds(3);

  //send the command
  data = SPI.transfer(sendByte);
  delayMicroseconds(3);            //There is also a minimum time after clocking that CS should remain asserted before we release it
  setCSLine(encoder, releaseLine); //if releaseLine is high set it high else it stays low

  return data;
}

/*
   This function sets the state of the SPI line. It isn't necessary but makes the code more readable than having digitalWrite everywhere
   This function takes the pin number of the desired device as an input
*/
void setCSLine(uint8_t encoder, uint8_t csLine)
{
  digitalWrite(encoder, csLine);
}

/*
   The AMT22 bus allows for extended commands. The first byte is 0x00 like a normal position transfer, but the
   second byte is the command.
   This function takes the pin number of the desired device as an input
*/
void setZeroSPI(uint8_t encoder)
{
  spiWriteRead(AMT22_NOP, encoder, false);

  //this is the time required between bytes as specified in the datasheet.
  //We will implement that time delay here, however the arduino is not the fastest device so the delay
  //is likely inherantly there already
  delayMicroseconds(3);

  spiWriteRead(AMT22_ZERO, encoder, true);
  delay(250); //250 second delay to allow the encoder to reset
}

/*
   The AMT22 bus allows for extended commands. The first byte is 0x00 like a normal position transfer, but the
   second byte is the command.
   This function takes the pin number of the desired device as an input
*/
void resetAMT22(uint8_t encoder)
{
  spiWriteRead(AMT22_NOP, encoder, false);

  //this is the time required between bytes as specified in the datasheet.
  //We will implement that time delay here, however the arduino is not the fastest device so the delay
  //is likely inherantly there already
  delayMicroseconds(3);

  spiWriteRead(AMT22_RESET, encoder, true);

  delay(250); //250 second delay to allow the encoder to start back up
}

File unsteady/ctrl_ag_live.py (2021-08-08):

#import serial
#import time
#import create_plot
#import matplotlib.pyplot as plt
#from matplotlib.animation import FuncAnimation
#import pandas as pd
#from itertools import count
import csv
from threading import Thread
import subprocess

filename = 't1.csv'
fieldnames = ["t", "angle", "iteration"]
#filename = str(input('Enter trial name:\n'))
#filename = set_filename()

#writing csv headers
with open(filename, 'w') as csv_file: #move to thread.py
    csv_writer = csv.DictWriter(csv_file, fieldnames=fieldnames)
    csv_writer.writeheader() #add ability to write to specific data folder

t1 = Thread(target=subprocess.run, args=([ "python", "control_ag2.py"],))
t2 = Thread(target=subprocess.run, args=([ "python", "create_plot.py"],))

t1.start()
t2.start()
t1.join()
t2.join()

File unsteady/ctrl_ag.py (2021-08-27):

# Daniel Asadi
# Eng Sci 2T3
# FCET Lab, UTIAS

import serial
import time
import csv
from datetime import datetime
from threading import Thread
import matplotlib.pyplot as plt
import pandas as pd
import math
import subprocess
import os

# EDIT FOLLOWING VARIABLES BEFORE RUNNING
matlab_freq = 0.178797
caseNo = '1790'
extraInfoFilename = ''  # add info such as _2 for a 2nd trial
filename = 'data/'+caseNo+'/'+caseNo+extraInfoFilename  # also change file name in create_plot_phase.py
valveDuration = 2
wireDuration = 2
encTrigAngle = 0
extraCamDelay = 0


def controlValve(ser):
    ser.write(b'A')  # high
    print('VALVE OPEN')
    time.sleep(valveDuration)  # valve duration
    ser.write(b'B')  # low
    print('VALVE CLOSED')


def controlCam(ser, syncDelay):
    time.sleep(syncDelay)
    ser.write(b'C')  # high
    time.sleep(0.1)
    ser.write(b'D')  # low
    print('CAM RECORD')
    time.sleep(0.1)
    ser.write(b'C')  # high
    time.sleep(0.1)
    ser.write(b'D')  # low
    print('CAM READY')


def controlWire(ser):
    ser.write(b'E')  # high
    print('WIRE ON')
    time.sleep(wireDuration)  # wire duration
    ser.write(b'F')  # low
    print('WIRE OFF')


def controlCap(ser):  # not included in circuit yet
    ser.write(b'G')  # high
    print('CAP DISCHARGED')
    time.sleep(1)  # discharging duration
    ser.write(b'H')  # low
    print('CAP CHARGING')


def readEnc(loops, filename, freq):
    completed = False
    t_list = []
    angle_list = []
    iteration_list = []
    trigT = 0

    p = 1/freq
    cDelay = 0.2  # cam trigger delay
    recDelay = cDelay + extraCamDelay  # can add delay here
    NcycDelay = math.ceil(recDelay/p)
    syncDelay = NcycDelay*p-cDelay  # delay to sync trigger at 0 deg

    print('READING AND SAVING DATA...')
    start = datetime.now().timestamp()

    for i in range(loops):
        line = ser2.readline()  # read a byte
        if line:
            try:
                # updating values
                s = line.decode()  # convert the byte string to a unicode string
                s2 = s.strip('\r\n')
                angle = int(s2)
                ser2.reset_input_buffer()
                ser2.reset_output_buffer()

                i += 1
                end = datetime.now().timestamp()
                t = round(end-start, 5)  # update time
                t_list.append(t)
                angle_list.append(angle)
                iteration_list.append(i)

                if encTrigAngle <= angle <= encTrigAngle+1 and not completed and i >= 500:  # trigger
                    t1 = Thread(target=controlCam, args=(ser, syncDelay,))
                    t2 = Thread(target=controlWire, args=(ser,))
                    t1.start()
                    t2.start()
                    trigT = t + NcycDelay * p - cDelay + 0.2
                    print('Cam triggered at: '+str(trigT)+' s')
                    completed = True

                if completed and (t > (trigT+5)):
                    break
            except ValueError:
                print('ERROR')

    if not completed:
        print('ERROR, position range not detected')

    print('Finished')  # post-processing

    while True:
        try:
            print()
            setting = int(input('Continue: [1]\nRetry: [2]\n'))
            break
        except ValueError:
            print('ERROR')
    if setting == 1:
        testFrame = float(
            input('Enter time for frame of interest to test accuracy from PFV4:\n'))
        phaseTestStart = trigT + testFrame
        print('Start of phase:', trigT, 's')
        print('Start of test phase of interest:', phaseTestStart, 's')

        create_csv(filename, t_list, angle_list, iteration_list)
        create_plt(filename)
        create_txt(filename, trigT, freq)
        emergencyStop(ser)


def create_csv(filename, t_list, angle_list, iteration_list):
    iteration = 1
    fieldnames = ["t", "angle", "iteration"]
    filename = filename+'.csv'

    with open(filename, 'w') as csv_file:
        csv_writer = csv.DictWriter(csv_file, fieldnames=fieldnames)
        csv_writer.writeheader()

    # writing to csv
    for (t, angle, iteration) in zip(t_list, angle_list, iteration_list):
        with open(filename, 'a') as csv_file:
            csv_writer = csv.DictWriter(
                csv_file, fieldnames=fieldnames)
            info = {
                "t": t,
                "angle": angle,
                "iteration": iteration
            }
            csv_writer.writerow(info)


def create_plt(filename):  # convert time axis to phase
    data = pd.read_csv(filename+'.csv')
    plt.rcParams['font.size'] = '4'
    x = data['t']
    y = data['angle']
    plt.xlabel('Time [s]')
    plt.ylabel('Encoder angle [deg]')
    x_plt = []
    if_append = 0
    index_plt = 1

    for t in x:
        if if_append:
            x_plt.append(t)
            if_append = 0
            index_plt = 1
        else:
            index_plt += 1
            if index_plt == 20:
                if_append = 1

    plt.xticks(rotation=60)
    plt.xticks(x_plt)
    plt.plot(x, y, linewidth=1)
    fig = plt.gcf()
    fig.set_size_inches(6.4, 3.6)
    plt.savefig(filename+'.png', dpi=300)
    plt.show()


def create_txt(filename, trigT, freq):
    f = open(filename+'.txt', 'w')
    f.write('Measured frequency: '+str(freq) +
            ' Hz vs matlab '+str(matlab_freq)+' Hz\n')
    f.write('Trigger start at 0 deg: '+str(trigT)+' s\n')
    f.close()
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

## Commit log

2021-06-28 Files from summer research internship at the FCET lab in UTIAS
    [8020-4136-BLACK.SLDPRT, C-Channel.SLDPRT, Calibration_Target.SLDPRT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]
2021-07-03 Temporarily removed encoder input
2021-07-03 Code for Arduino Mega to read output and send inputs
2021-07-03 Code for Arduino Uno to read outputs and send inputs
2021-07-03 Code for Arduino Mega to read outputs and send inputs, encoder output temp commented
2021-07-03 Code for reading Encoder output with Arduino from AMT
2021-07-03 Python control codes for smoke flow viz components
2021-07-03 Version 1 Arduino code
2021-07-07 Arduino code
2021-07-22 Arduino code for communication to circuit components
2021-07-23 Added 2nd arduino just to read encoder inputs which does not affect the other arduino's serial buffer
2021-07-23 Added in 2nd arduino, now fully functional for active grid usage
2021-07-23 Did some tests, not needed currently
2021-07-23 moved encoder zeroing location in code which was causing issue
2021-07-27 Updated circuit diagram
2021-08-03 Working on adding encoder graphing features
2021-08-03 Converted encoder values to angle values
2021-08-08 Misc files
    [t1.csv]
2021-08-08 Updated code to read and save encoder data while triggering smokeflow
2021-08-10 Temp changes to resolve timing issues
    [t1.csv]
2021-08-10 Fixed timing issues
    [t1.csv]
2021-08-10 Fixed delays and data recording issues
    [case1671.csv, t1.csv]
2021-08-11 Added saving data to Data file, added filenaming feature
    [case1671.csv, case1671_5k.csv, case1672_3k.csv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]
2021-08-13 Added frequency calculation feature, took some trials but phase angle and freq are still incorrect
    [1673.csv, 1673b.csv, case1671_5k.csv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]
2021-08-13 Fixed loop timing issue cont version, only delay and freq calculation is incorrect
    [1673.csv, 1673b.csv, test.csv]
2021-08-13 Convert time axis to phase and find correct delay
    [ctrl_ag.py, ctrl_ag_cont.py]
2021-08-13 Small filename fix
    [test1673.csv]
2021-08-14 Added first set of data, ctrl_ag_cont is working correctly, just need to add function to calculate f before
    [1671.csv, 1672_2.csv, 1673.csv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]
2021-08-15 Update ctrl_ag.py
    Updated x-axis in create_plt to display the encoder angle as a function of phase angle in degrees instead of as a function of time
2021-08-15 Update ctrl_ag_cont.py
    Updated create_plt to display encoder angle as function of phase angle instead of as function of time
2021-08-16 Update create_plot.py
    Updated x-axis
2021-08-16 Updated phase calculation, still need to fix an issue, ctrl_ag now calculates freq before
    [create_plot_phase.py, ctrl_ag.py]
2021-08-16 Organized data, ctr_ag_cont has some fixes but is still older version
    [1671.csv, 1672_2.csv, 1673.csv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]
2021-08-16 New data, small fixes
    [1681.csv, 1682.csv]
2021-08-17 Added new data
    [1672.csv, 1683.csv, 1683b.csv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]
2021-08-17 Small fixes, cont mode is now updated version
    [ctrl_ag.py, ctrl_ag_cont.py]
2021-08-23 fixed filename issue
    [1671.csv, 1672.csv, 1673.csv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]
2021-08-23 Update create_plot_phase.py
    Figured what was wrong with plot making (frequency was being overestimated by noise at beginning), edited it to delay by almost one cycle to get rid of noise in frequency calculation
    [create_plot_phase.py]
2021-08-23 fixed freq calculation issue, starting phase plotting
    [create_plot_phase.py, ctrl_ag.py, ctrl_ag_cont.py]
2021-08-23 got phase data for all except 1681
    [1671.csv, 1672.csv, 1673.csv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]
2021-08-23 Update create_plot_phase.py
    Added functionality for case 1681 because it has a vertical line in it
2021-08-23 did phase plot for 1681, final feature to add is delay between encoder reading and writing to csv and capacitors
    [1681.csv]
2021-08-27 More unsteady cases taken
    [1786.csv, 1787.csv, 1788.csv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]
2021-08-27 Low freq cases
    [1790.csv, 1790_0deg.csv]
2021-08-27 Added catching error exceptions, made extra fixes for smooth usage
    [create_plot_phase.py, ctrl_ag.py, ctrl_ag_cont.py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]
2021-09-09 Added camera manual files
